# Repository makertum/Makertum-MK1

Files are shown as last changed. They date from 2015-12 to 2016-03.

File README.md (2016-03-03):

# Makertum MK1 - a 230 / 110 V~ PCB Heated Bed
The Makertum MK1 is a mains voltage heated bed for 3D printers with dual voltage support (230/110 V~), 500 W of heat output, 2 minutes heatup time (110 °C), power indicator LED and onboard thermal fuse. It is currently available to skilled beta testers all over the world.

render of top side
render of bottom side

## Caution
- this is highly experimental
- do not use this if you don't know what you're doing
- don't hold me responsible for the outcome of what you do with the information in this repository
- even if operated electrically correct this device is dangerous and can get hot enough to seriously injure humans and animals.

## Project status and compatibility
- [x] layoutet basic MK1 design
- [x] compatible to MK2/B heated bed in terms of dimensions / mounting hole spacing
- [x] compatible to most MK2/B heated beds in terms of endstop position
- [x] added 110 and 230 V~ compatibility by wiring options
- [x] added thermal fuse
- [x] added LED overcurrent fuse
- [x] added warnings, wiring and instructions to the silkscreen
- [x] added milled polycarbonat led/fuse cover
- [x] picked license [CC-BY-NC-SA](http://creativecommons.org/licenses/by-nc-sa/3.0/legalcode)
- [x] manufactured beta batch on FR4
- [x] stress tested beta batch (FR4) on 110 °C for 30 days, no visible damage, no deformation, observed slight darkening of solder mask
- [x] stress tested beta batch (FR4) on 130 °C for 30 days, no visible damage, no deformation, observed slight darkening of solder mask and slight yellowing of silkscreen
- [x] started shipping beta kits to beta testers now (get yours on [makertum.com/en/shop](http://www.makertum.com/en/shop))
- [ ] beta testing is in progress, but not completed
- [ ] cannot be considered safe yet, be cautious

## Specifications
- Power consumption:	500 W (230 V~) or 460 (110 V~) (beta PCBs may differ)
- Operation Voltages:	230 V~ (110 V~ over a center tap)
- Resistance:	~106 Ω (beta PCBs may differ)
- Trace length: about 402 x 200 mm = ~80,800 mm
- Copper thickness (on PCB):	1oz aka 1.37 mil aka 35 µm
- Trace width:	0.37 mm
- Safety features: onboard thermal fuse, fused power indicator LED with protective polycarbonat cover
- Mounting Holes: 209 mm center-to-center (RepRap compatible) + 3-point leveling

## Documentation
Board layout and BOM can be found in this repo, extensive assembly instructions are maintained on [hackaday.io](https://hackaday.io/project/8671/instructions)

## How to use
[RTFM](https://hackaday.io/project/8671/instructions). Know what you do. Solder components as described in the BOM, make sure no excess solder can cause shorts of any kind. Wire as instructed on the backside of the PCB, do not use without professional supervision and appropriate safety precautions. Do not use without closed loop temperature control, i.e. with a thermistor/thermocouple and SSR, since the thermal fuse is supposedly a safety feature rather than a means of temperature control.

## Why?
There are many benefits of a mains voltage PCB heated bed: I will be driven directly from mains, skips the need for an expensive power supply, high current heatsinked SSR and heavy wire. Instead, it can be driven by a cheap low current SSR without heatsink. It's also cheaper to manufacture and provides more structural support for your printing plate than silicone heater pads.
IMHO, it’s pretty much nuts to convert down mains voltage in a power supply to 12/24V just to drive a heating element, except that it „feels“ a bit safer. Also, it’s a false assumption, that a 12/24 V heated bed is actually safe, since in case of an unexpected malfunction it will still burn down your place - regardless of the voltage on the heating element. Using fuses, temperature feedback and considering failure scenarios cannot be omitted anyway.

## Disclaimer
I am not responsible for the outcome of what you do with this information. As said, this is a highly experimental and untested prototype.

## License
Created by Moritz Walter 2015, released under [CC-BY-NC-SA](http://creativecommons.org/licenses/by-nc-sa/3.0/legalcode)

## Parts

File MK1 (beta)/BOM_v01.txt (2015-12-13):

STRUCTURAL
1x PCB, 1oz copper clad
1x (big/small)_led_cover_top milled from clear polycarbonat
1x (big/small)_led_cover_bottom milled from polycarbonat
1x piece of kapton tape or thermal compound for attaching thermistor
2x M2 screw (length depends on cover config)
2x M2 nut

ELECTRONIC COMPONENTS
1x thermo fuse MTS 133, switching temperature 133 °C, øxl = 4x12 mm [Ftemp]
2x SMD LED 0805 [LED1/LED2]
1x SMD resistor 0805, 1 kΩ [Rled]
1x Picofuse 0,063 A http://cdn-reichelt.de/documents/datenblatt/C400/PICO_ESK.pdf [Fled]
1x thermistor
1x 5x20mm 3A slow blow fuse
1x DA-Solid State Relay (SSR), min. 5 A, recommended 20 A

WIRING
5x cable lug M3
5x conductive aluminium/brass M3 screw
5x conductive aluminium/brass M3 nut
5x piece of shrinking tube to insulate cable lugs
1x piece of power wire for bridging, min. AWG 24
2x power connection wires, min. AWG 24
1x thermistor connection wires
1x 5x20mm cable current fuse holder

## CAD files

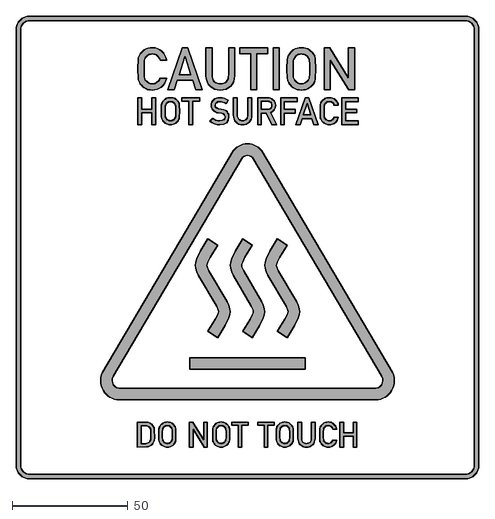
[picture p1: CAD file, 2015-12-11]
MK1 (beta)/Graphics/caution_v01.dxf
199.9 x 200.0

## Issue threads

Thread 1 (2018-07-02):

what is the dimension of the bed?

amrithmmh, 2018-07-02:
what is the dimension of the heaterbed and can it be scaled to 1000mmx1000mm for big 3d printer build?

amrithmmh, 2018-07-11:
please reply

fajardocj, 2018-12-12:
+1, pls respond

benhadad, 2021-06-07:
The bed cannot be directly scaled as this will change the resistance of the traces. A new layout would be required.

amrithmmh, 2021-06-07:
thank you. appreciate it!

Closed 2021-06-07.

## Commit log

2015-12-13 added cable current fuse
2016-03-03 added Gerbers, MK1 dir
    added Gerbers and created MK1 version directory
    [caution_v01.dxf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]
